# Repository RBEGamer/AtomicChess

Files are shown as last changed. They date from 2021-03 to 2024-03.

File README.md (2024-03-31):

# AtomicChess - The most advanced self playing chess table

prod

## FEATURES

This automated chess table allows the user to play chess using real pieces over the internet with other chess tables or via a web client.
The chess table acts as an opponent and can move the pieces automatically and recognizes the player's moves and sends them to the opponent (chess table or virtual). 

| | Atomic Chess Table |
|:---|---:|
| Recognition figure position | yes, using NFC tags under figures |
| Connectivity | LAN, WLAN |
| Automatic movement of the figures | yes |
| Game Livestream | yes |
| Game history and player scoring | yes |
| Cloud connection (online games) | yes, central gameserver and matchmaking |
| Parking position for eliminated figures | yes |
| Stand-alone functionality | yes, using stockfish-11 (player profile dependent playing strength) | 
| Special features | voice control (Amazon Alexa), DGT3000 chess clock integration, customizable figures |

### OTHER PROJECTS COMPARISON

#### COMMERCIAL PRODUCTS

| | Square Off-Kingdom | Square Off-Grand Kingdom | DGT-Smart Board | DGT Bluetooth Wenge |
|:---|---|:---:|:---:|---:|
| detection figure position | no (manual) | no (manual) | yes | yes |
| Dimensions (LxWxH) | 486mm x 486mm x 75mm | 671mm x 486mm x 75mm | 540mm x 540mm x 20mm | 540mm x 540mm x 20mm |
| Connectivity | Bluetooth | Bluetooth | Serial | Bluetooth |
| automatic movement of the figures | yes | yes | no | no |
| Game Livestream | yes | yes | yes | yes |
| Cloud connection (online games) | yes (App) | yes (App) | yes (PC) | yes (PC + App) | 
| parking position for eliminated characters | no | yes | no | no |
| stand-alone functionality | no (App required) | no (App required) | no (PC) | no (PC) | 
| special features | battery for 30 games | battery for 15 games | - | -  

#### OPENSOURCE PROJECTS
| | Automated Chess Board | Automated Chess Board | DIY Super Smart Chessboard |
|:---|:---:|:---:|---:|
| Figure Position Detection | no (manual) | yes (camera) | no |
| dimensions (LxWxH) | no specification | no specification | 450mm x 300mm x 50mm  |
| connectivity | USB (PC required) | WIFI | |
| automatic movement of the figures | yes | no | | |
| game livestream | no | no | |
| cloud connection (online games) | no | no | yes |
| Parking position for eliminated figures | no | no | no |
| stand-alone functionality | no (PC required) | yes | yes |
| special features | - | voice control | train display (LED matrix)  | |

## Integration of an embedded system into a cloud infrastructure using the example of an autonomous chess table

**NOTE**
This project is my bachelor thesis in computer science. The thesis (german) with details is also available in this repository.

ATC_PROD_TABLE_FINAL_IMG_orig

### Abstract

The goal of the work is to develop an autonomous chess table, which is able to move chess pieces autonomously and to react to user interactions. The core question of the thesis thus relates to the verification of the feasibility including the creation and implementation of an embedded system and a cloud infrastructure. The focus is especially on the programming of the embedded system and the interaction of this with a server accessible from the Internet, which serves as an intermediary between different manholes and other end devices.

First, the approaches existing at the time and their implementation are examined. Here, particular attention was paid to illustrating the limitations of existing systems and comparing them to functions that only apply to this project. From the results, the requirements of the autonomous shaft table are derived, which are to be implemented in this work.

Subsequently, two prototypes were implemented iteratively one after the other, which differ strongly from the mechanical design as well as the electrical one. The developed software, on the other hand, was developed modularly so that it can be used on both prototypes. The different designs are due to the fact that in the first iteration of the autonomous chess table, after an endurance test, numerous potential improvements were identified. This led to a complete redesign in the second iteration and thus an autonomous shaft table was developed, which fulfills all requirements.

Basically, it should be noted that the result of the work is not a finalized product, but a structural prototype. Further tests, such as usage statistics or safety tests, would have to be carried out before the shaft table can be considered a commercial product.

The system and especially the implemented cloud service can be accessed and extended online. Among other things, this allows building your own table using the AtomicChess system, but also integrating other components. Experienced developers can thus expand the game at will or even add to other games. The mechanics and game management designed for the project can accordingly also be used for various other table board games.

### PAPER PDF

`./documentation/atomicchess_thesis.pdf`

### CITE

```tex
@software{Ochsendorf_Marcel_AtomicChessBA_2021,
author = {Ochsendorf, Marcel},
license = {GPL-2.0},
month = {9},
title = {{Integration of an embedded system into a cloud infrastructure using the example of an autonomous chess table}},
url = {https://github.com/RBEGamer/AtomicChess},
version = {1.0.0},
year = {2021}
}
```

## PICTURES


 


## IDEAS

* chess.com & lichess.org integration
* possible target position lights

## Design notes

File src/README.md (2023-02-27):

# SRC

## FOLDER STRUCTURE

* src_atctest => Contains a simple Buildroot Test Package
* src_buildroot => Contains the buildroot source with docker build scripts
* src_ci => Contains the Jenkins server and configuration files
* src_controller => Contains the main chess table controller
* src_marlinfw => Contains the firmware for the used SKR1.3 and SKR1.4 motor controller boards
* src_mechanic => Contains all CAD files for the different hardware revisions
* src_server => Contains the complete game server, player ai server and the CI setup
* src_shared => Contains all used 3rd party libraries and the custom made IPC library (guicommunicator)
* src_thesis => Contains the thesis document and a thesis publishing server
* src_dgt3000chessclockextention  => Contains the DGT 3000 Chess-Clock extention software for the DGT PI
* src_userboardcontroller  => Contains the atmega328p nfc reader to serial bridge software used for prod 1,2 models

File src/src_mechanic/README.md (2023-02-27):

# SRC_MECHANIC

This folder contains all mechanical drawings (CAD, SVG, STL files). During development three hardware revisions were developed.

## USED TOOLS

* FDM 3D Printer (Ender 3 Pro, Ender 2)
* Soldering Iron (Weller PU81)
* Hex Keys / Allen Wrenchs
* Hotglue Gun

* [OPTIONAL] SLA 3D Printer (Elegoo Mars 2 Pro) for custom Chess Figures 
* [OPTIONAL] Crosscut Saw (Bosch GCM8) for Item cutting
* [OPTIONAL] Lasercutter (K40E) for acryl chess board markings

## HARDWARE REVISIONS

* `HARDWARE_PROD_V2` => Contains the final version with CoreXY configuration. For this a control board (SKR) with Marlin needed. Firmware in `src_marlinfw`. 

* `HARDWARE DEV` => Contains the IKEA Lack Table version of the chess table using self developed hardware and pcbs and a two coil system.

## NOTES

The software `atc_controller` and `atc_qtui` is compatible with all versions of the hardware.
The only difference is the configuration file `atccontrollerconfig.ini` which need modification to the new board size and controller type (SPI or Marlin).
If not configuration file is present the table automaticly generates a default one for the selected version.

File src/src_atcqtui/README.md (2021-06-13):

# AtomicChessOS

# BRANCH - QTUI

This folder contains the QT5 User Interface which is running on the RaspberryPi Display.

## REQUIREMENTS
For this chapter the following requirements must be met:

* Crossplattform toolchain and target images is build. The `/buildroot/output/host` folder is accessable on the development system.
* Embedded device is flashed with the image and reachable over SSH.
* `Qt Creator >= 4.10` and `Qt Design Studio` is installed on the development system (`>= Ubuntu 16.04`).

## TASK OF THE UI

The main purpose of the ui is the management of a gameand should not stand in 
* simple editable
* provide simple menu structure with max two menu layers
* player browser
* start game /stop game

### MENUS

## Qt

### WHY Qt

### QML

#### QML COMPONENTS

Every element begins with the type name of the qml component `Text {`, in this case its a label component.
The following block can contain at least a `id` attribute, but can have many more attributes.
The most common attributes are the  position on the screen `x`, `y` and a size `width`, `height`.
These attributes are automaticly added, if an element is created with the visual editor in `Qt Creator` or `Qt Design Studio`.

In case of the label, some additional attributes are nedded.
The `text` attribute, sets the visibal text of the label and the font size can be changed with the `font.pixelSize` attributes.

```qml
Text {                                          //QML TYPE, Text means label                                          
            id: hb_label                        //ID OF THE ELEMENT
            objectName: "hb_label"              //NAME TO ACCESS THE LABELS ATTRIBUTES IN C++ BACKEND
            x: 318                              //POSITION IN SCREEN COORDIANTES
            y: 18                   
            width: 164                          //SIZE
            height: 34
            text: qsTr("MAIN MENU")             //VISIBLE TEXT
            visible: true                       // HIDE| SHOW ELEMENT
            font.pixelSize: 30                  //FONTSIZE OF THE TEXT
        }
```

The next element which is heavily used in the UI for the project, is a simple button.
In addition to the already shown attributes, a new section called `Connections` was added to the element.
Most of the qml types can emit events, if a state of the element changes.
For example, the button can emit the `onClick` event, if the user clicked on the button.
A eventlistener can be registered in a `Connections {` block.
This block needs a `target` attribute, which value is the `id` of the element, the events should be processed.

The eventlistener itself is a function, which has the name of the event `onClick`.
The systax is JavaScript based and a small subset of the JavaScript language in functions is supported.

```js
onClick: {
            var arr = ["My", "Label"] //JS ARRAY
            hb_label.text = arr[0] + arr[1] //ACCESSING ATTRIBUTE OF AN OTHER QML ELEMENT
            console.log("CLICKED!") //JS EXPRESSION
        }
```
A complete QML Javascript refrence guide can be found on the Qt 5 Site.
[QML_JS_REFERENCE](https://doc.qt.io/qt-5/qtqml-javascript-expressions.html)

The goal of our button example is if the user clicked on the button, the label with id `hb_label` should be displayed.
Also a function from an other QML Componente should be called, in this example the `main_menu` component is our C++ backend.

```qml
Button {
            id: hb_button
            x: 731
            y: 4
            width: 61
            height: 61
            text: qsTr("BUTTON NAME")
            //REGISTER EVENT HANDLERS
            Connections {
                target: hb_settings_button      //FOR WHICH ELEMENT ID IS THE CONNECTION             
                function onClicked(_mouse){     //EVENT HANDLER FOR THE CLICK EVENT
                    hb_label.visible = true     //MODIFY OTHER QML ELEMENTS
                    main_menu.lb_settings_btn() //CALL A C++ BACKEND FUNCTION (main_menu is the QML instance of the C++ backend)
                }
            }
        }
```

### MOCKUP

For the first mockups, the tool `Balsamique Mockup 3` was used to create a wireframe model of the menus.
Though the requirement that the userinterface should be simple to create and operate, only simple GUI element was used (like buttons, labels, icons).
So the userinterface can be adapted in every other UI framework too.
It also habe to be simple to use for the user and every menu should only present the most important elements.

The UI conzept offers the users to do the following things:

* Start a random game
* Start a game with selected user
* Overview of game progress and state
* Abort game
 
After deciding which elements are necessary to map this functionality, a simple mockup of the user interface was created.

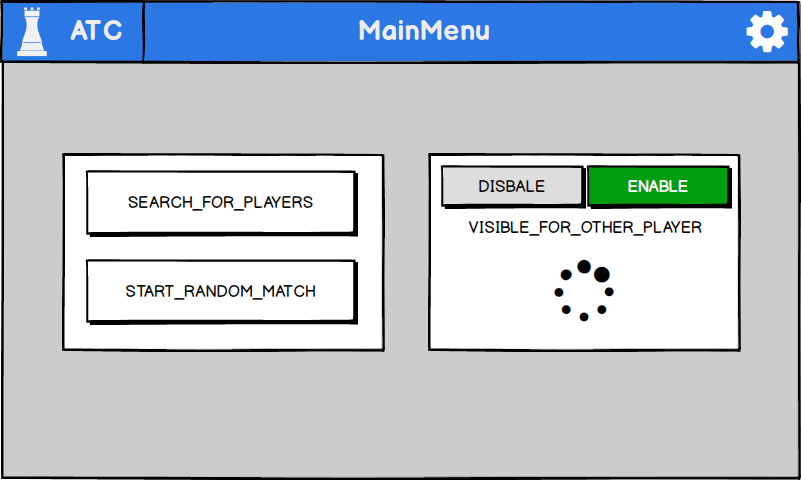
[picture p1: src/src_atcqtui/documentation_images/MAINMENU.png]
MOCKUP_MAIN_MENU


For example, this is the mockup of the MainMenu. It allowes the player, to start a random game, get the players list and a spinning indicator was used to show the state of the game search funktion.

The gearbox icon, redirects the user to the settings menu. This menu offers basic options to interact with the table.
In a normal usage situation this settings menu is not important, but it is mostly used for maintenance.
The settings menu is accessable in every other menu and the back button, redirects the user back to the last menu showed before opening the settings menu.

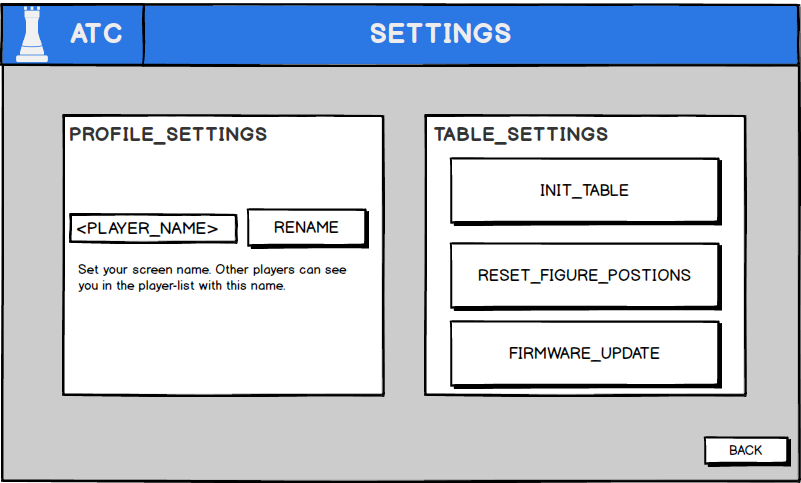
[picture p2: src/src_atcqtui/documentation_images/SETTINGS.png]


A general information menu was added, which shows the table software version, its hardware id (used for communcation with the cloud backend).
For debug reasons the last internal errormessage can be shown here.

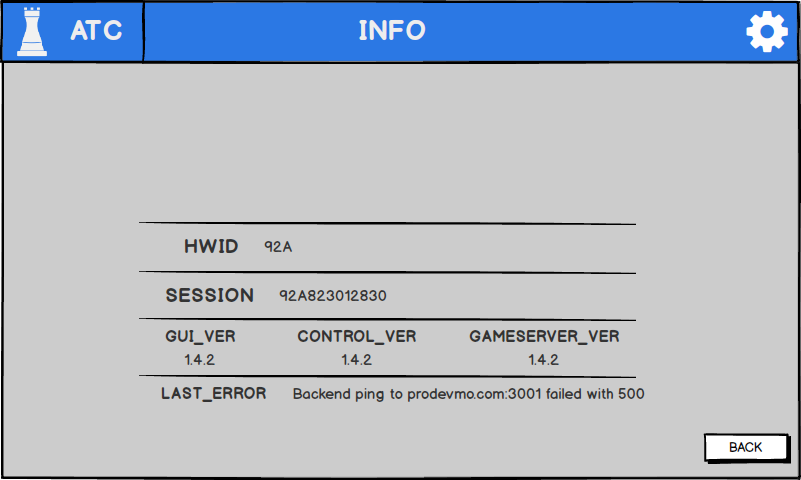
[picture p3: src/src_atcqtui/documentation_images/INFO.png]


This are only three example menus created for the user interface.
After creating the mockups, `Qt Design Studio` was used to convert the Mockup into an `QML` represenation

### Qt Design Studio

`Qt` offers several different tool to create a user interface. In this case the `Qt Design Studio`, was used in the first step of implementing the UI form the mockup. It has some advantages over the `Qt Creator`, reagarding the design workflow. It is for example possible to direclty import Adobe Photoshop files, this feature was used for the creation of the icons used in the interface. No manually export of the icon from Adobe Photoshop and reimporting into Qt was needed.
It supports live preview of the design as an running application, no compilation needed for reviewing the UI.

The software uses a simple drag&drop system for elements, like buttons, labels and self designed components. The element can be placed on a empty screen to build the ui from the ground up. It provides integration for the `QtQuickControl II` component presets, which includes some more advance ui element like the animated spinner or progress bars.

While building the UI in the software, the equivalent QML code is generated which corresponds in an `.qml` file.
The QML file can now be loaded into a `Qt Quick - Application` project inside of the `Qt Creator` software. 

## Qt Creator

* works without QtCreator but offers features espacially for editing C++ and QML files together
### PROJECT SETUP
* simply clicking ok; but choose qmake
* generate main.cpp with qml loading code ; and a basic qml file 
### TOOLCHAIN SETUP
* path setup
### DEVICE SETUP
* add device with ip address

## QML `objectName` ATTRIBUTE
It is also possible to edit the QML code and add new QML components inside of `Qt Creator`, which offers a QML visual editor.
Here all object which are designed to be changed with C++ code, become a unique name. This happens inside of the QML code with the `objectName` attribute.

For example the content of the version label on the info menu should be changeable, so its gets a unique name with 
```qml
Text {
            id: is_hwid_label
            objectName: "is_hwid_label"
            x: 358
            y: 54
            color: "#ffffff"
            text: qsTr("HWID")
            font.pixelSize: 30
        }
```

With the `objectName` attribute set, it is possible modify other attributes inside of the element.
In the following C++ function is taken from the `menumanager.cpp` which is the C++ backend class between the QML and the `InterProcessCommunication`.
The funktion changes the visible attribute of an element, which is searched with the `objectName` attribute.

```c++
//menumanager.cpp
void MenuManager::set_visible_element(QString _name, bool _state){
    QObject* obj = this->parent()->findChild<QObject*>(_name);
    if(obj){
        obj->setProperty("visible",_state);
    }else{
        qInfo()<< "cant get element" << _name;
    }
}
```
## QML C++ BACKEND

As mentioned above, the UI is controlled by a C++ backend, it connects the QML UI with the `InterProcessCommunication` class.
This backend can be used as a normal QML Component, but allowes all C++ feature can be used to control the UI.
The backend is a normal C++ Class, but it have to inherited from `QObject`.

```c++
//menumanager.h
#include <QObject>
class MenuManager: public QObject
{
```

After creating the class files `menumanager.h` and `menumanager.cpp`, the last step is to register the new created class as a usable QML component.
This happend in the `main.cpp` file directly after bevore loading the QML file with the `qmlRegisterType` function call.

```c++
//menumanager.h
#include "menumanager.h"
int main(int argc, char *argv[])
{
            QGuiApplication app(argc, argv);
            QWindow window;
            window.setBaseSize(QSize(800,480));
            ...
            ...
            
            //REGISTER THE TYPE MenuManager WITH THE NAME MenuManager AND VERSION 1.0 AS QML TYPE WITH NAME MenuManager           
            qmlRegisterType<MenuManager>("MenuManager",1,0,"MenuManager");
            
            //LOAD QML FILE AND DISPLAY IT
            QQuickView view;
            view.engine()->addImportPath("qrc:/qml/imports");
            view.setSource(QUrl("qrc:/qml/WINDOW.qml"));
            ...
            ...
```

The last step required is to use the new created QML type in the QML file `WINDOW.qml` of the UI.

```qml
//qml/WINDOW.qml
Rectangle {
    id: window
    objectName: "window"
    width: 800
    height: 480

    //CREATE AN ELEMENT OF QML TYPE MenuManager    
    MenuManager{
        id:main_menu
    }
```
Now every function inside of the UI can call functions in the C++ backend by using the ID `main_menu.<FUNCTION>()`.

### ACCESS MODIFIERS TO WORK WITH THE UI
In the headerfile `menumanager.h` function can be declared with the access modifiers, for example`public` or `private`.
In the Qt C++ there are other modifiers avariable, espacially for connecting with QML.

The mainly used modifier for this project is the `public slots` modifiert. Each function declared in this section can be called from the QML side.

```c++
//menumanager.h
class MenuManager: public QObject
{
public slots:
            void trigger_login_event_button(); //call if login button is pressed
```

For example the obve delcared function `trigger_login_event_button` should be called with a button in the QML UI is pressed by the user.

```qml
qml/WINDOW.qml
Button {
            id: hb_button
            ... //OTHER ATTRIBUTES
            //REGISTER EVENT HANDLERS
            Connections {
                target: hb_settings_button      //FOR WHICH ELEMENT ID IS THE CONNECTION             
                function onClicked(_mouse){     //EVENT HANDLER FOR THE CLICK EVENT
                    
                    main_menu.trigger_login_event_button() //CALL A C++ BACKEND FUNCTION (main_menu is the QML instance of the C++ backend)
                    
                }
            }
        }
```
[SIGNALS_SLOTS_QT](https://doc.qt.io/qt-5/signalsandslots.html)

### GET EVENTS FROM QML COMPONENTS | REACT TO BUTTONS
With the `public slots` modifiers above, its is now possible to react to event from components.
For example if the user presses the login button.
In the `mainmenu` class, for each action is a function declared, mostly for buttons an their `onClick` event.

```c++
//menumanager.h
class MenuManager: public QObject
{
...
...

public slots:
// ----- HEADLINE BAR ---- //
    void lb_settings_btn();         //ONCLICK EVENT FOR SETTINGS ICON
    void lb_info_btn();             //ONCLICK EVENT FOR INFO ICON                     
    // ----- LOGIN/START ----//
    void ls_login_btn();            //ONCLICK EVENT FOR START BUTTON                       
    ...
```

Every functions triggers a event, which are send to the rest of the system by using the `Inter Process Communication` class.

```c++
//menumanager.cpp
void MenuManager::ls_login_btn(){
    qInfo() <<"ls_login_btn"; //DEBUG MESSAGE
    
    //CREATE EVENT WITH ACTION TYPE (GUI_ELEMENT::BEGIN_BTN) AND THE TYPE OF EVENT (GUI_VALUE_TYPE::CLICKED)
    guiconnection.createEvent(guicommunicator::GUI_ELEMENT::BEGIN_BTN, guicommunicator::GUI_VALUE_TYPE::CLICKED);
}
```

### MODIFY QML COMPONENTS | SWITCHING BETWEEN MENUS

Now its possible to react to user events, but the other direction, to send events to the gui is needed.
To display the current gamestate or switching between menus.

The `visible` attributes of an element, defines if the element is visible on the ui or not.
In the case of the UI for this project. Each menu is placed inside of an container.
If the user open a specific menu, all other menus will be hidden by setting the `visible` attribute to `false`, ecept of the target menu.

For this purpose each menu container has its own `objectName` attribute.

* `mm_container`, is the main menu container
* `ss_container`, is the settings menu container
* `ls_container`, is the start screen container

To finally switch the a menu the function `switch_menu(QString _container_name)` can be used, for simple menu switching.
It poulates a variable called `last_menu_opened`, this stores the menu name the user comes from and makes its possible to switch back to the previous menu.
This functionally comes handy, for the settings menu, which can be opened from every other menu and by closing the settings menu the user redirect back to the previous menu.

```c++
switch_menu("ls_container"); //SHOW LOGIN MENU
switch_menu("ss_container"); //SHOW SETTINGS MENU
switch_menu(last_menu_opened); //SWITCH BACK TO LOGIN MENU (= PREVIOUS MENU)
```

For this menu structure it is sufficient to store only the previous menu.
A queue is used to enable navigations with deeper menu structures.

```c++
//menumanager.h
QStack<QString> menu_visist_history;
QMap<QString, int> menu_levels;
QString current_menu = "";

//menumanager.cpp
//ENTER MENU
void enter_menu(QString _name){
            previous_menus.push(current_menu)
            current_menu = _name;
            switch_menu(current_menu);
}

void leave_menu_to_previous(e){
    qInfo() << "go_menu_back";
    if(menu_visist_history.isEmpty()){ //CHECK IF PREV MENU EXISTS
        return;
    }
    QString tmp = menu_visist_history.pop(); //LOAD PREV MENU
    switch_menu(tmp); //SWITCH TO PREV MENU
}

void MenuManager::switch_menu(QString _screen){
    //SAVE ONLY THE CURRENT SCREEN TO THE QUEUE IF WE MOVE A LEVEL UP IN SCREEN TREE
    if(menu_levels.contains(_screen) && menu_levels.contains(current_menu_opened) && menu_levels[_screen] > menu_levels[current_menu_opened]){
    menu_visist_history.push(current_menu_opened);
    qInfo()<< "added to history " << current_menu_opened;
    }
    current_menu_opened = _screen;
    //...
    //...
}
```

### INTER PROCESS COMMUNICATION

The whole `Inter Process Communication` acronym `IPC` functionallity was implemented in `guicommunicator` class, which is located in the `SHARED` folder.

The `guicommunicator` offers a bidirectional communication between processes, which is needed for communcation between the UI and the controller software.
There a already implementations for such a behavior like `gRPC`, `librpc` or message queues like `ZeroMQ`.

??
TYPES
??

For this project a own implementation for the `IPC` concept was created. One reason for that was the integration into the buildroot system.
`gRPC` has a bug in the package compilation with buildroot.
A issue on the `libabseil-cpp` library GitHubPage, was opended.

ISSUE

An alternative to `gRPC` is the `ZeroMQ` library, which offers a lightweight message queue concept.
Buildroot offers libraries for building the `ZeroMQ` message broker and different client libraries `libzqm`.
Both packages are build into the toolchain.

`ZeroMQ` is designed for performance message transportation (10.000 message in 15ms) ,which is not needed for this project.

[ZeroMQ_PERFORMANCE](http://wiki.zeromq.org/area:results)

The `guicommunicator` class offers two methods for the message transport:

* `ZeroMQ`, by using the define `USE_ZMQ_AS_IPC`
* `Webserver`, by using the define `USE_WEBSERVER_AS_IPC`

The webserver method is implemented by using a http client and webserver instance for each direction.
This method was used, because the UI was designed before the other software parts.
So as other 'process' a simple http client can be used.

The codebase is for the UI and the Control apllication is the same.
There are some differences, Qt uses its own string type `QString` and uses other debug features `QDebug()`.
For this cases defines are used to implement the same function for both the Qt version and non Qt version.
The deine `USE_QT` is set in the project settings of the Qt project.

```c++
//SHARED/guicommunicator.h
#ifdef USES_QT
            #include <QString>
            #include<QDebug>
            #include <QThread>
            #include <QMutex>
#else
            #include <string>
            #include <mutex>
            #include <iostream>
            #include <thread>
#endif
```

In the implementation of the functions, the define was used.

```c++
//SHARED/guicommunicator.cpp
	void guicommunicator::createEvent(GUI_ELEMENT _event, GUI_VALUE_TYPE _type) {
		guicommunicator::createEvent(_event, _type, (std::string)"");
	}
#ifdef USES_QT 
	void guicommunicator::createEvent(GUI_ELEMENT _event, GUI_VALUE_TYPE _type, QString _value) {
		guicommunicator::createEvent(_event, _type, _value.toStdString());
	}
#endif
```

The `guicommunicator` class offers two main methods:

* `createEvent(_event, _type, _value)`, to send a event to the other process.
* `GUI_EVENT get_gui_update_event()`, which returns the received events

The library uses a thread for sending and received message packets, so start and stop methods are implemented.
The calling of this methods are only necessary if the instance of class want to receive messages.

* `start_receive_thread`, start receive thread.
* `stop_receive_thread`, stop receive thread.

After receiving a message (from webserver or `ZeroMQ`), the message will be checked and converted into the `GUI_EVENT` struct.
Allo received messaged will. be queued up into an queue datastructure and can pulled of the queue by using the `get_gui_update_event` method.
The insertion and reading of the queue, is secured with an binary semaphor to avoid a condition race in the critical section.
The critical section is in this case, the read/write access to the queue.

* TYPES OF EVENTS

* PACKING OF THE MESSAGES -> protobuf

##### Protobuf
* message types
* needed information
* generation of the .proto file to cpp code
* location of the files in shared folder

##### Webserver
* advantage for debugging
* zeromq not wokring

### DEPLOYMENT

* using buildroot pacakge
* simply use qmake to gerneate makefile
* and run makefile in buildroot
 
## CONCLUSION

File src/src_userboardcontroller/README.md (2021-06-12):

# SRC_USERBOARDCONTROLLER

Contains the Arduino-Sektch for the PN532 to Seriell converter, to connect the nfc reader to the controller via usb

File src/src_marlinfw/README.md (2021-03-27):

# SRC_MARLINFW

This directory contains the used Marlin-Firmware for the SKR1.3 (HWREV_PROD1) and SKR1.4_TURBO (HWREV_PROD2).

The simplest way to compile and flash the narlin firmware is with Visual Code and the following installed Plugins:

* PlatformIO
* Auto Marlin

## PRECOMPILED MARLIN FIRMWARE

Simply copy the .bin file to the SD Card of the board, or via the USB mount.

* SKR1.3 => ./SKR_V1.3_BOARD_FIRMWARE/ATC_HWREV_PROD1_MODIFIED_FIRMWARE/
* SKR1.4_TURBO => ./SKR_V1.4_BOARD_FIRMWARE/ATC_HWREV_PROD1_MODIFIED_FIRMWARE/

## MARLIN SOURCE PROJECTS

* SKR1.3 => ./SKR_V1.3_BOARD_FIRMWARE/BTT SKR V1.3/firmware/Marlin-bugfix-2.0.x
* SKR1.4_TURBO=> ./SKR_V1.4_BOARD_FIRMWARE/BTT SKR V1.4/firmware/Marlin-2.0.x-SKR-V1.4-Turbo/

## USED GCODE COMMAND

The controller software uses the following GCode commands. Some are optional for example the M150 command that setup the RGB Strip.

### REQUIRED COMMANDS
* `G21` - set units to mm
* `G90` - absolute positioning
* `G28` - home axis
* `M280` - set servo
* `G0` - move linear
* `M400` - wait for action finished

* `M260 M261` - i2c read write (for nfc read)

### OPTIONAL COMMANDS

* `M84` - disable steppers
* `M502` - reset eeprom
* `M500` - write config to eeprom
* `M92` - set steps/mm
* `M150` - set rgb led strip color

## IMPORTANT CONFIGRATION SETTINGS IN MARLIN-FW

The main marlin configuration files are the `Configuration.h` and `Configuration_adv.h` located in the the Marlin folder.

For the ATC Project the following settings are changed in comparision with the default config.

### Configuration.h

* `0615 | #define COREYZ //ON HWREV_PROD2`  
* `0664 | #define X_MIN_ENDSTOP_INVERTING true // Set to true to invert the logic of the endstop.`
* `0665 | #define Y_MIN_ENDSTOP_INVERTING true // Set to true to invert the logic of the endstop.`
* `0750 | #define DEFAULT_AXIS_STEPS_PER_UNIT   { 80, 80, 400, 93 } // FOR HWREV_PROD2 USE { 100, 100, 400, 93 }`
* `1096 | #define INVERT_X_DIR false //INVERT ENDSTOP SIGNAL`
* `1097 | #define INVERT_Y_DIR false` 
* `1132 | #define X_BED_SIZE 700`
* `1133 | #define Y_BED_SIZE 700`
* `1404 | #define HOMING_FEEDRATE_XY 600 //LIMIT THE HOMING FEEDRATE`
* `2359 | #define NEOPIXEL_LED //ENABLE NEXOPIXEL LED SUPPORT`
* `2365 | #define NEOPIXEL_PIXELS 60       // Number of LEDs in the strip.`
* `2412 | #define NUM_SERVOS 1 // Servo index starts with 0 for M280 command ON SKR BOARD THE SERVO PIN IS P2_00`
* `2417 | #define SERVO_DELAY { 500 } //(ms) Delay  before the next move will start`

### Configuration_adv.h

`2797 | #define EXPERIMENTAL_I2CBUS //ENABLE I2C Master`

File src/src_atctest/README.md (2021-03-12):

# ATC_TESTPACKAGE

This program is a compile and install test for the modified buildbrocess of the buildroot framework.
This folder will be fetched from the buildroot atc_testpackage package configured in buildroot.

Please see the `./src/src_buildroot/packages/atctp` directory for the actual build configuration.

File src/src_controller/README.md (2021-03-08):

# AtomicChessOS

# ATC CONTROLLER

The controller is the main system on the embedded device that controls the hardware of a ATC Table

* Motor Control
* Communcication with the Server
* Communication with the UI running on the device
* Chess Figure Movement Algorithm

For this software component, we are using a Windows and Visual Studi environment for developing the software.
Our embedded system is a linux device, so we have to build the application for the linux environment running on the emmbedded device.
For this task, the prevously build buildroot toolchain is used.
A software plugin called VisualGDB for Visual Studio, enable Visual Studio to use the linux toolchain over a remote linux system, in order to build and deploy the application.

## REQUIREMENTS

* windows pc for development
* linux pc with buildroot toolchain
* embedded system for deployment

## SETUP A PROJECT USING VISUAL STUDIO AND VisualGDB

### REQUIREMENTS

On the development windows pc is the following software installed:
* Windows 10 Pro x64
* Visual Studio 2019 (Community or Enterprise)
* VisualGDB Plugin (Version 5.5, Linux Edition)
* A SSH Client (MobaXterm Personal Edition)
* git (Gitkraken)

### LINUX BUILD SYSTEM

On the linux build system, the VisualGSB plugin builds the project.
The system is a `Intel Nuc 10`, mini pc, with a stock `Ubuntu 20.04` installed.
One the machine are all package requirements for building the buildroot toolchain installed (see buildroot chapter).

After cloning the repository `$ git clone -b buildroot git@github.com:RBEGamer/AtomicChessOS.git ./atc_buildroot` and switched to the `buildroot` branch, the build process of the toolchain was invoked using the build script `$ ./atc_buildroot/src/src_buildroot/buildroot/build.sh`.

After building the  toolchain is completed, the further configuration work can be done on the windows development pc.
Its nessessary for the linux build system to allow SSH connections.
Its may required to install the OpenSSHServer uisng `$ sudo apt install openssh-server`.

The VisualGDB plugin requires some extra packages on the build pc:

* `$ sudo apt-get install socat`

Now the configuration of the linux build pc for the VisualGDB plugin is complete.
The next step, is the setup of the embedded system for deployment.

### EMBEDDED SYSTEM DEPLOYMENT

Afer building the sources into an executable, the final binaries will be copied to the embedded system.
The embedded system is flashed with tha latest image build by buildroot.

In order to setup the VisualGDB Project, its nessessary that the embedded device can be accessed over SSH.

#### MAKEFILE MODIFICATIONS
* buildroot build oveerrides TARGETNAME AND CONFIG to load a different makefile config in order to use the toolchain generated by buildroot
The different configurationa are stored in different .mk files that will be includes by the Makefile.
THe `debug.mk` configuration contains theVisualGDB Configuration that allows the Visual Studio Plugin to use the remote toolchain on the linux server and can only build by over the visual gdb plugin.
The `release.mk` configuration is used to build the controller apllication with the buildroot framework. It used the compiler executable paths defines by $CC. $LD enviroment variables and build the program with release flags and without any debug symbols. All used libraries are linked staticly.

## THIRD PARTY LIBRARIES

The ATC_Controller software uses serveral different third party libraries, escacially for http requests and json parsing.
* `https://github.com/nlohmann/json#serialization--deserialization`, json parsing.
* `https://github.com/yhirose/cpp-httplib`, http/https requests.
* `https://github.com/Neargye/magic_enum`, enum handling.
* `https://github.com/emilk/loguru`
A copy of the used versions, are located in the controller software directory.

# CONTROLLER OVERVIEW

## MOTOR DRIVER
## BOARD CLASS

## CHESS PIECE
### NFC TAG CONTENT GENERATOR
Each figures NFC tag is ued to identify the figure. For easy usage of the NFC tag, it is formatted into the NDEF format, so its simply possible to program the NFC tags with an mobile phone. The tag contains a ndef `text record` with a string to identifiy the type of figure (three bits), color (one bit) and a counting number (four bits). A combination of all three attributes make the figures id unique to the system. For the automatic unique ID generation, a html page `ChessFigureIDGenerator.html` was created to automaticliy generate all ID for a complete chess board.
Only one byte is stored in the record of the text record and so only 10bytes are used on the NFC tag.

* MSB [7,6,5,4,3,2,1,0] LSB 
* MSB [TYPE,TYPE,TYPE,COLOR,ID,ID,ID,ID] LSB 

For reading the NFC tag with the PN532, the program only reads the first NDEF record and parses the text record data to get the figure type. With this system it is possible to expand the system further and store more data on the NFC tag, by adding more NDEF records.

On the controller side two functions were created to generate the unique ids and read them back.

```c++
  ChessPiece::FIGURE fig;
	fig.figure_number = 1;
	fig.color = ChessPiece::COLOR_BLACK;
	fig.type = ChessPiece::TYPE_KNIGHT;
  
  //GENERATE ID FROM STRUCT
  uint8_t UNIQUE_ID = ChessPiece::figure2NDEF(fig);
  
  //PARSE UNIQUE_ID BACK TO A STRUCT
  ChessPiece::FIGURE back = ChessPiece::NDEF2Figure(UNIQUE_ID);
  
````
* IMAGE

## CONFIG AND CALIBRATION

The system uses a config file located in the filesystem `/usr/ATC/atccontroller.ini`.

### CALIBRATION

In order to calibrate the mechanic, several entries in the config file has to be changed.

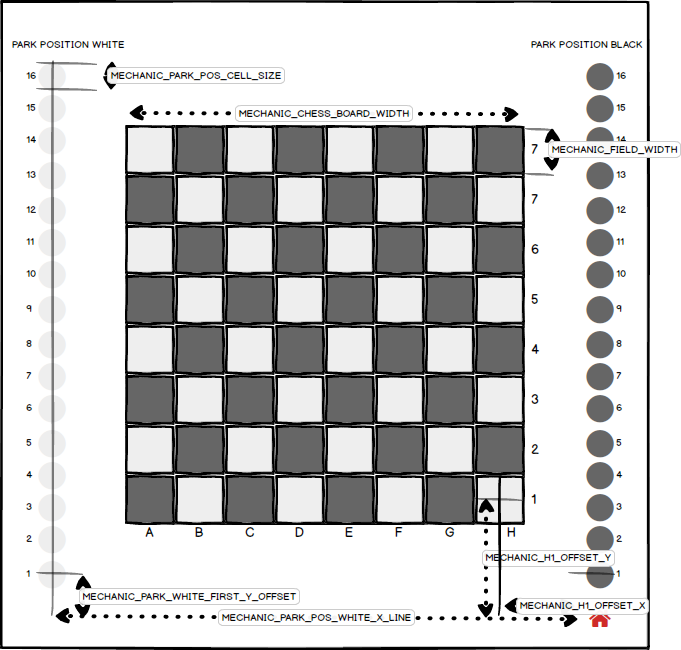
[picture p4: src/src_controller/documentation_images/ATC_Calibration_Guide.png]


### Chess Piece Movement Algorithm

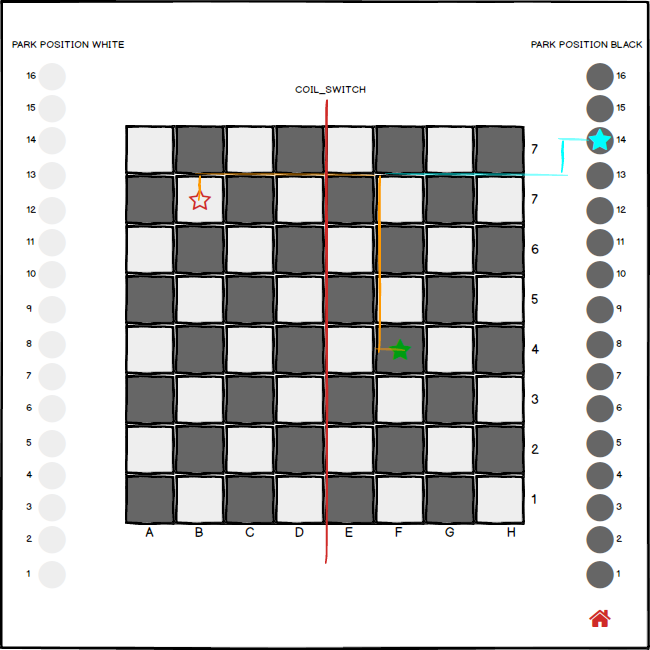
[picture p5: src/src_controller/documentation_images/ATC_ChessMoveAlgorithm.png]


#### BASIC MOVEMENT PROCEDURE

*move 
##### BOARD <-> BOARD

##### PARK_POSITION <-> BOARD || BOARD <-> PARK_POSITON

##### ALGORITHM IMPROVEMENTS

* queue movement all movementinstructions needed for a move, send them combinded to the motor driver
* send coil change event only if changed, SPI Implementation needs time (about 0.5 Secs with the wait ACK)
*

#### PIECE MOVE TIME

| ALGORITHM_V1_TRAVEL_TIME [s] 	| ALGORITHM_V2_TRAVEL_TIME [s] 	| TRAVEL_DISTANCE [FIELDS_DIAGONAL] 	|
|---	|---	|---	|
| 7.20 	| 2.56 	| 1 	|
| 11.56 	| 6,20 	| 3 	|
| 12,27 	| 7,06 	| 5 	|
| 14,39 	| 6,56 	| 8 	|

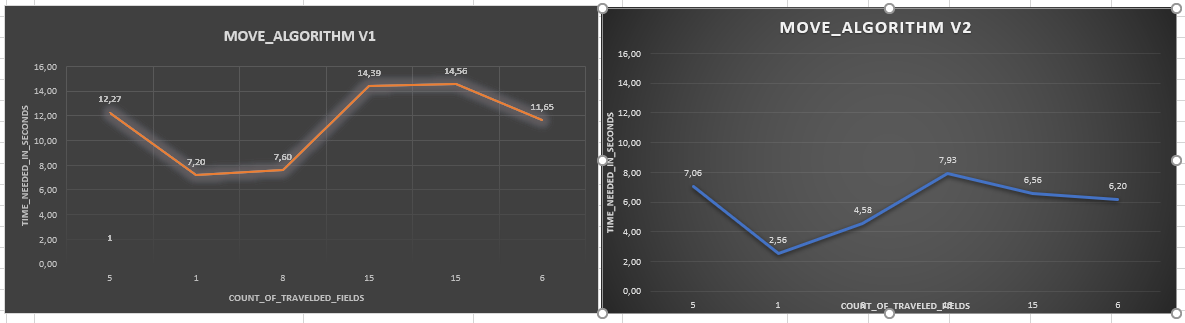
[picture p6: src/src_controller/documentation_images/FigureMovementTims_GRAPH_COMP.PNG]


### MOVEMENT SPEED COMARPISION HARDWARE V1 / V2
* gocde slower nicht

#### [LINUX] HANDLING DIFFERENT 
The simplified hardware design of the projects uses two USB2Serial adapters to connect the SKR1.3 Stepper Driver Board and the User-Move Dector with the Embedded System. All serial deives will be mount under the `/dev/ttyXXX` path and the the squence can be differ after each reboot. In order to prevent this, it is possible to mount a usb device with a Vendor and Product-ID to a specified path using a custom udev roule.
For each rule, the Vendor and Product-ID is needed, for this commands like `lsub` or `usb-devices` and output the relevant information for each usb device attached.
```
$ usb-devices

T:  Bus=03 Lev=02 Prnt=02 Port=02 Cnt=03 Dev#= 11 Spd=12  MxCh= 0
D:  Ver= 2.00 Cls=ef(misc ) Sub=02 Prot=01 MxPS=64 #Cfgs=  1
P:  Vendor=1d50 ProdID=6029 Rev=01.00
S:  Manufacturer=marlinfw.org 
S:  Product=Marlin USB Device
S:  SerialNumber=06FF800AAF3D08075C664F58F50020C3
C:  #Ifs= 3 Cfg#= 1 Atr=80 MxPwr=500mA
I:  If#=0x0 Alt= 0 #EPs= 1 Cls=02(commc) Sub=02 Prot=00 Driver=cdc_acm
I:  If#=0x1 Alt= 0 #EPs= 2 Cls=0a(data ) Sub=00 Prot=00 Driver=cdc_acm
I:  If#=0x2 Alt= 0 #EPs= 2 Cls=08(stor.) Sub=06 Prot=50 Driver=usb-storage
```
During development, several different board are used to control the different hardware sections.
These can be divided into two main groups :

* `Stepper-Controller` - For controlling the Stpper-Drivers, Endstop, Coils/Servo
* `User-Move-Detector` - To interface the hall-sensor array, to detect a manual move of the figures.

In the following table, the Vendor/Product-IDs from some tested boards are listed below:

| Product | SUBSYSTEM | Vendor-ID | Product-ID | SYMLINK | Board-Type |
|---|---|---|---|---|---|
| Bigtreetech SKR 1.4 Turbo | tty | 1d50 | 6029 | ttySKR | Stepper-Controller |
| Bigtreetech SKR 1.3 | tty | 1d50 | 6029 | ttySKR | Stepper-Controller |
| Arduino Due [Programming Port]  | tty | 2341 | 003d | ttyUBC | User-Move-Detector |
| Arduino Due [Native SAMX3 Port] | tty | 2341 | 003e | ttyUBC | User-Move-Detector |
| CH340 | tty | 1a86 | 7523 | ttyUBC | User-Move-Detector |
| HL-340 | tty | 1a86 | 7523 | ttyUBC | User-Move-Detector |
| STM32F411 | tty | 0483 | 5740 | ttyUBC | User-Move-Detector |

With these information, is is possible to generate the needed udev rules.
```
$ cat /etc/udev/rules.d/50-usb.rules

...
SUBSYSTEM=="tty", ATTRS{idVendor}=="1d50", ATTRS{idProduct}=="6029", SYMLINK+="ttySKR"
...
SUBSYSTEM=="tty", ATTRS{idVendor}=="0483", ATTRS{idProduct}=="5740", SYMLINK+="ttyUBC"
...
```
This configuration archieves, that any type (of supported) Stepper-Controller-Boards are accessable over the `/dev/ttySKR` symblink.

After the installation of the rules and connection of a SKR1.3 and a STM32F411 (known as STM32-BlackPill), the device directory contains the following entires:

```
ls /dev/tty*

/dev/ttyS27  /dev/ttyS6
/dev/ttyUSB0  /dev/ttyACMA0  /dev/tty25  /dev/tty32  /dev/tty4  /dev/ttyprintk  /dev/ttySKR  /dev/ttyUBC
```
The in the configutation file of the controller file, these tty paths are set and no reconfiguration for different hardware configuration is needed.

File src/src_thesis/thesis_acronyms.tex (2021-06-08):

\makeglossaries
\newacronym{ic}{IC}{Integrated Circuit}
\newacronym{html}{HTML}{Hypertext Markup Language}
\newacronym{js}{JS}{JavaScript}
\newacronym{css}{CSS}{Cascading Style Sheets}
\newacronym{ndefrtd}{NDEF-RTD}{NDEF Record Type Defintion}
\newacronym{http}{HTTP}{Hypertext Transfer Protocol}
\newacronym{https}{HTTPS}{Hypertext Transfer Protocol Secure}
\newacronym{ftp}{FTP}{File Transfer Protocol}
\newacronym{dns}{DNS}{Domain Name System}
\newacronym{aws}{AWS}{Amazon Web Services}
\newacronym{nfc}{NFC}{Near Field Communication}
\newacronym{rfid}{RFID}{Radio-Frequency Identification}
\newacronym{ci}{CI}{Continuous Integration}
\newacronym{cd}{CD}{Continuous Deployment}
\newacronym{iot}{iot}{Internet of Things}
\newacronym{mqtt}{mqtt}{Message Queuing Telemetry Transport}
\newacronym{rest}{REST}{Representational State Transfer}
\newacronym{api}{API}{Application Programming Interface}
\newacronym{cad}{CAD}{Computer-Aided Design}
\newacronym{rpi}{RPI}{Raspberry-Pi}
\newacronym{os}{OS}{Operating System}
\newacronym{vcs}{VCS}{Version Control System}
\newacronym{atc}{ATC}{Atomic Chess Table}
\newacronym{ui}{UI}{User Interface}
\newacronym{gui}{GUI}{Graphical User Interface}
\newacronym{ssh}{SSH}{Secure Shell}
\newacronym{ntp}{NTP}{Network Time Protocol}
\newacronym{sftp}{SFTP}{Secure File Transfer Protocol}
\newacronym{ide}{IDE}{Integrated Development Environment}
\newacronym{ipc}{IPC}{Interprocess Communication}
\newacronym{qml}{QML}{Qt Modeling Language}
\newacronym{dtb}{DTB}{Device Tree Binary}
\newacronym{dtc}{DTC}{Device Tree Compiler}
\newacronym{dtd}{DTD}{Device Tree Document}
\newacronym{ndef}{NDEF}{NFC Data Exchange Format}
\newacronym{gcc}{GCC}{GNU Compiler Collection}
\newacronym{gdb}{GDB}{GNU Debugger}
\newacronym{i2c}{I2C}{Inter-Integrated Circuit}
\newacronym{iic}{IIC}{Inter-Integrated Circuit}
\newacronym{spi}{SPI}{Serial Peripheral Interface}
\newacronym{usb}{USB}{Universal Serial Bus}
\newacronym{ufw}{ufw}{Uncomplicated Firewall}
\newacronym{pkg}{PKG}{Package}
\newacronym{ai}{AI}{Artificial Intelligence}
\newacronym{fdm}{FDM}{Fused Deposition Modeling}
\newacronym{sla}{SLA}{Stereolithography}
\newacronym{pla}{PLA}{Polylactic Acid}
\newacronym{abs}{ABS}{Acrylonitril-Butadien-Styrol-Copolymer}
\newacronym{tcp}{TCP}{Transmission Control Protocol}
\newacronym{udp}{UDP}{User Datagram Protocol}
\newacronym{stl}{STL}{Standard Triangle Language}
\newacronym{pcb}{PCB}{Printed Cirtcuit Board}
\newacronym{lan}{LAN}{Local Area Network}
\newacronym{wlan}{WLAN}{Wireless Local Area Network}
\newacronym{wan}{WAN}{Wild Area Network}
\newacronym{dc}{DC}{Direct Current}
\newacronym{ac}{AC}{Alternating Current}
\newacronym{iso}{ISO}{Internation Organisation for Standardization}
\newacronym{din}{din}{Deutsches Institut für Normung}
\newacronym{gpl}{GPL}{General Public License}
\newacronym{ble}{BLE}{Bluetooth Low Energy}
\newacronym{uci}{UCI}{Universal Chess Interface}
\newacronym{fen}{FEN}{Forsyth-Edwards-Notation}
\newacronym{xfen}{X-FEN}{Extended Forsyth-Edwards-Notation}
\newacronym{ajax}{AJAX}{Asynchronous JavaScript and XML}
\newacronym{hal}{HAL}{Hardware Abstraction Layer}
\newacronym{fifo}{FIFO}{First In – First Out}
\newacronym{json}{JSON}{JavaScript Object Notation}
\newacronym{led}{LED}{Light-Emitting Diode}
\newacronym{pwm}{PWM}{Pulse Width Modulation}
\newacronym{gpio}{GPIO}{General Purpose Input/Output}
\newacronym{id}{ID}{Identifikator}
\newacronym{cnc}{CNC}{Computerized Numerical Control}
\newacronym{tls}{TLS}{Transport Layer Security}
\newacronym{ssl}{SSL}{Secure Sockets Layer}
\newacronym{dhcp}{DHCP}{Dynamic Host Configuration Protocol}
\newacronym{udev}{UDEV}{userspace device file system}
\newacronym{hf}{HF}{high frequency}
\newacronym{uscf}{USCF}{United States Chess Federation}
\newacronym{dsi}{DSI}{Display Serial Interface}
\newacronym{hdmi}{HDMI}{High Definition Multimedia Interface}
\newacronym{gpu}{GPU}{Graphics Processing Unit}
\newacronym{cpu}{CPU}{Central Processing Unit}

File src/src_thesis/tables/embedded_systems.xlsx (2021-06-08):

 | Raspberry-Pi 3b+ | STM32MP157A-DK1
Prozessor | Arm Cortex-A53 | Arm Cortex A7 + Arm Cortex A4
Arbeitsspeicher | 1GB LPDDR2 SDRAM | 4-Gbit DDR3L
Flash-Speicher | SD-Karte | SD-Karte
(+gpio)-Header | ja (40 Pol, (+i2c),(+spi)) | ja (40 Pol, (+i2c),(+spi))
Netzwerkanschluss | (+lan), (+wlan) | (+lan), (+wlan)
Besonderheiten | 64-bit Prozessor | Arm Cortex A4 Co-Prozessor, Secure-Boot, Debugger
Disable Motors | M84 | X Y

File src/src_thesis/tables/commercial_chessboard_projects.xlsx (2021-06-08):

 | Square Off – Kingdom | Square Off - Grand Kingdom | DGT Smart Board | DGT Bluetooth Wenige
Erkennung Schachfigurstellung | nein (Manuell per Ausgangsposition) | nein (Manuell per Ausgangsposition) | ja (Resonanzspulen) | ja((+rfid))
Abmessungen (LxBxH) | 486mm x 486mm x 75mm | 671mm x 486mm x 75mm | 540mm x 540mm x 20mm | 540mm x 540mm x 20mm
Konnektivität | (+ble) | (+ble) | (+usb) / Seriell | Bluetooth 2.0
Automatisches Bewegen der Figuren | ja | ja | nein | nein
Spiel Livestream | ja | ja | ja | ja((+rfid))
Cloud anbindung (online Spiele) | ja (über Mobiltelefon + App) | ja (über Mobiltelefon + App) | ja (über PC + App) | ja (über PC + App)
Parkposition für ausgeschiedene Figuren | nein | ja | nein | nein
Stand-Alone Funktionalität | nein (Mobiltelefon erforderlich) | nein (Mobiltelefon erforderlich) | nein (PC erforderlich) | nein (PC erforderlich)
Besonderheiten | Akku für 30 Spiele | Akku für 15 Spiele | Bussystem | -

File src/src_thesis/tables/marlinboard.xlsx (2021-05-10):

 | SKR 1.4 Turbo | Ramps 1.4 | Anet A8 Mainboard
Stepper Driver | TMC2209 | A4988 / TMC2209 | A4988
LED Strip Port | WS2811 / RGB | - | -
Firmware | Marlin-FW 2.0 | Marlin-FW 1.0 | proprietary

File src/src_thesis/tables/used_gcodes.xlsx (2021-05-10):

 | G-Code Command | Parameters
Move X Y | G0 | X<dest_pos_x_mm> Y<dest_pos_y_mm>
Move Home Position | G28
Set Units to Millimeters | G21
Set Servo Position | M280 | P<servo_index> S<servo_position>
Disable Motors | M84 | X Y

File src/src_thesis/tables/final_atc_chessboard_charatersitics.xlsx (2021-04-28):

 | Atomic Chess – autonomous Chessboard
Erkennung Schachfigurstellung | ja
Feldabmessungen (LxBxH) | 57x57mm
Abmessungen (LxBxH) | 620x620x170mm
Gewicht | 5.7kg
Konnektivität | (+wifi), (+usb)
Automatisches Bewegen der Figuren | ja
Spiel Livestream | ja
Cloud anbindung (online Spiele) | ja
Parkposition für ausgeschiedene Figuren | ja
Stand-Alone Funktionalität | ja

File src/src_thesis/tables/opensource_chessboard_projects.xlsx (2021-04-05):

 | Automated Chess Board (Michael Guerero) [@actproject1] | Automated Chess Board (Akash Ravichandran) [@actproject2] | DIY Super Smart Chessboard [@actproject3]
Erkennung Schachfigurstellung | nein (Manuell per Ausgangsposition) | ja (Kamera / OpenCV) | nein
Abmessungen (LxBxH) | keine Angabe | keine | 450mm x 300mm x 50mm
Konnektivität | (+usb) / Seriell | Ethernet, (+wlan) | Ethernet, (+wlan)
Automatisches Bewegen der Figuren | ja | ja | nein
Spiel Livestream | nein | nein | nein
Cloud anbindung (online Spiele) | nein | nein | ja
Parkposition für ausgeschiedene Figuren | nein | nein | nein
Stand-Alone Funktionalität | nein (PC erfoderlich) | ja | ja
Licence | (+gpl) 3+ | (+gpl) | -
Besonderheiten | - | Sprachsteuerung (Amazon Alexa) | Zuganzeige über LED Matrix

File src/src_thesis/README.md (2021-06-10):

# AtomicChessThesis

Das eigentliche Dokument ist die `thesis_document.md`. Die finale PDF `thesis.pdf` ist soweit aktuell, wenn ich diese erstelle, dies ist hier im Repo noch nicht automatisiert.
Ein bauen per Dockerimage ist möglich mittels ` build_thesis_docker.sh` Script und erzeugt die `thesis.pdf` neu.

# CHANGELOG

# 10.06.2021

* final spelling, " ", code korrektur/check
*

# 08.06.2021

* 4.2 - Auswahl des eingebetteten Systems (neu)
* Tabellen Fix (neu) für Tabelle 2.1 und Tabelle 2.2

# 07.06.2021

* einarbeitung Kommentare (neu)

# 05.06.2021

* 7.3 Service: Backend - Matchmaking+Beispiel (bearbeitet)
* 7.3 Service: Backend - Docker-Compose Code (bearbeitet)

# 04.06.2021

* Abstract - thesis_abstract.md (neu)
* 9.0 Anhang entfernt (neu)

# 02.06.2021

* einarbeitung Kommentare (neu)
* 4.0 Machbarkeitsanalyse und Verifikation ausgewählter Technologien (neu)

# 31.05.2021

* anpassungen Bilder (überarbeitet)
* abstract (neu)
* Zusammenfassung Kapitel 4 +5 => Machbarkeitsanalyse und Verifikation ausgewählter Technologien
* 4 Machbarkeitsanalyse und Verifikation ausgewählter Technologien (neu)
* 4.1 ErprobungBuildroot-Framework (neu)
* 4.2 Verifikation NFC Technologie (neu)
* 4.3 Schrittmotor/Schrittmotorsteuerung (neu)
* 8.0 Embedded System Software (neu)

# 30.05.2021

* 10 - Fazit (neu)
* 10.1 - persoenliches Fazit (neu)
* 10.2 - Ausblick (neu)

# 28.05.2021

* 8.2 - Service Architektur (neu)
* added Haskel to Dockerfile
* added csv2table pandoc filter
* added bib ref for docker, redis, mongo, docker-compose

# 27.05.2021 

* anpassungen Bilder (überarbeitet)

# 26.05.2021 II

* 8.4 - Backend (neu)

## 26.05.2021 I

* 1.1 - Motivation (überarbeitet)
* 6.1 - Mechanik (Bild eingefügt)
* 7.2 - Optimierungen der Spielfiguren (Bild eingefügt)
* 7.5 - Fazit bezüglich des finalen Prototypens (neu)

## 25.05.2021 II

* einarbeitung Kommentare 11:49
* einfügen Referenzen für Tabellen

## 25.05.2021 I

* 6.5 - Fazit des ersten Prototypens
* 7.1.1 - Gehäuse und Design
* 7.1.2 - 3D-Komponenten
* 7.1.3 Positions-Mechanik
* 9.1 - Ablaufdiagramm
* 9.2 - Figur Bewegungspfadberechnung

## 24.05.2021

* 6.3 - Schaltungsentwurf
* 6.4 - Implementierung HAL
* 7.1 - Modifikation der Mechanik

## 23.05.2021

* pandoc chapter numbering fix
* delaration, abstract toc fix
* pcb, schematic img added

## 21.05.2021 - INITIALE VERSION

* 3 - Einleitung, Motivation, Methodik
* 4.1 - 4.3, Analyse
* 5.4 - 3D Druck
* 6.1 - 6.2, Mechanik
* 7.2 - 7.3 - Optimierungen HWRev 2, HAL
* 8.5 - 8.7 - AutoPlayer WebClient
* 9.3 - 9.4 IPC User-Interface

## BUILD THESIS thesis_document

`$ bash ./build_thesis_docker.sh`

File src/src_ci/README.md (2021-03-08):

## Continous Integration

### WHY CI

### ADVANTAGES IN THIS PROJECT

For debugging and testing, building, checking the result, doing these step manually is okay.
But after the basic setup is working, the next task is to automate this tasks.
Especially, becuase the build process of buildroot can take serveral hours and the development pc is working hard to accomplish this task.
A good solution is outsource this task to a dedicated server. With an installed CI system on the server its not nessessary to kick off the process manualy.

The end result should be:

* Developer commits changes to release branch
* CI System detect changes and starts build process
* After successful build, save build artefacts
* (Publish build artefacts to production system)

In the case of building an sd card image for the embedded system, a manual step is needed to get the build files from the CI system running. So the CI can not publish the artefact to a production system. A better solution in this task is, to notify the developer that a build is succeed.

In this chapter we are getting to setup the jenkins software and create a configuration for the buildroot project in order to build the images for the embedded system automaticly.

### WHAT IS JENKINS

### SETUP JENKINS BLUEOCEAN

For this setup, the server is a virtual machine hosted on AWS (Amazon Web Service). Here is used a `AWS EC2 t3.2xlarge` instance.
This instance type offers 8 cpu threads and 32GiB of RAM. The Harddrive-Storage is here not important, the network troughput too.
As virtual machine base image (OS), we choose Amazon Linux which is based on Debian Linux.
It has a basic setup and ships with preinstalled applications like Docker, it is also hardened about remote root access.

This virtual machine is used to host the Jenkins Master, Build-Agents and the ATC_Server.

#### INSTALL JENKINS BLUEOCEAN

The setup of the jenkins software is very easy though the usage of Docker.
Jenkins offers a Docker-Image which can be installed though the `docker-cli`:

* `$ docker --version`, checks if docker is installed.
* `$ docker container run --name jenkins-blueocean --network host --env DOCKER_HOST=tcp://docker:2376 -v $(pwd)/jenkins_conf:/var/jenkins_home -p 8080:8080 -p 50000:50000 --restart always jenkinsci/blueocean`, pull docker image and start a new container using this image.

##### SITENOTE CONTAINER MANAGEMENT

Its possible to manage all docker container thought the `docker-cli`. There is also a webinterface for manage them, called portainer.
The portainer-webinterface allows to start/stop/create containers, image repository management and gives detailed logs and statistics over running containers.
Portainer is also able to manage a docker swarm or stack environment. In this reason portainer was also used to manage the docker environment on the remote server from the development pc.

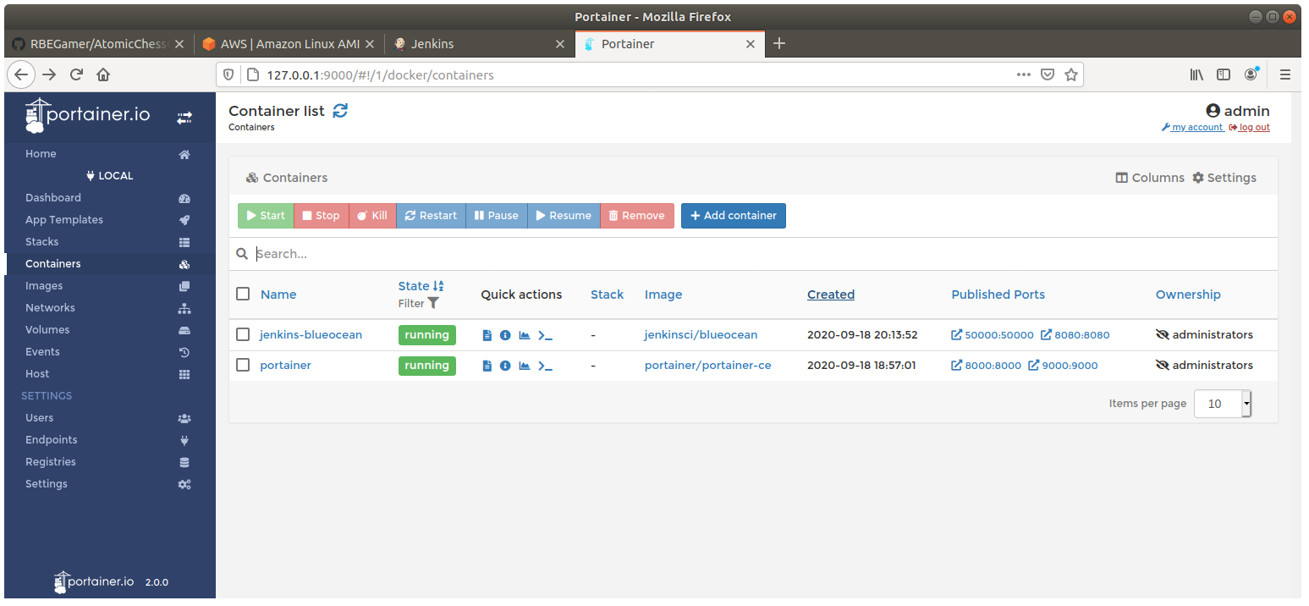
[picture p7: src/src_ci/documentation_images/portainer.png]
PORTAINER


The installation of portainer is very simple:

* `$ docker volume create portainer_data`, creates a volume for configuration data.
* `$ docker run -d -p 8000:8000 -p 9000:9000 --name=portainer --restart=always -v /var/run/docker.sock:/var/run/docker.sock -v portainer_data:/data portainer/portainer-ce`, start the portainer container. Its important to mount the local docker environment to the container using `-v /var/run/docker.sock:/var/run/docker.sock`.

The webinterface can be accessed with an brower pointing to `http://127.0.0.1:9000/`.

##### END SITENOTE

The Container needs two ports to be opened to the outside. On port `8080` the webinterface that jenkins provide can be accessed.
After successful start og the container, its possible to access the webinterface with the browser `http://127.0.0.1:8080/`.

The next steps are some basic installation questions:

* Install recommended plugins
* Setup a user account

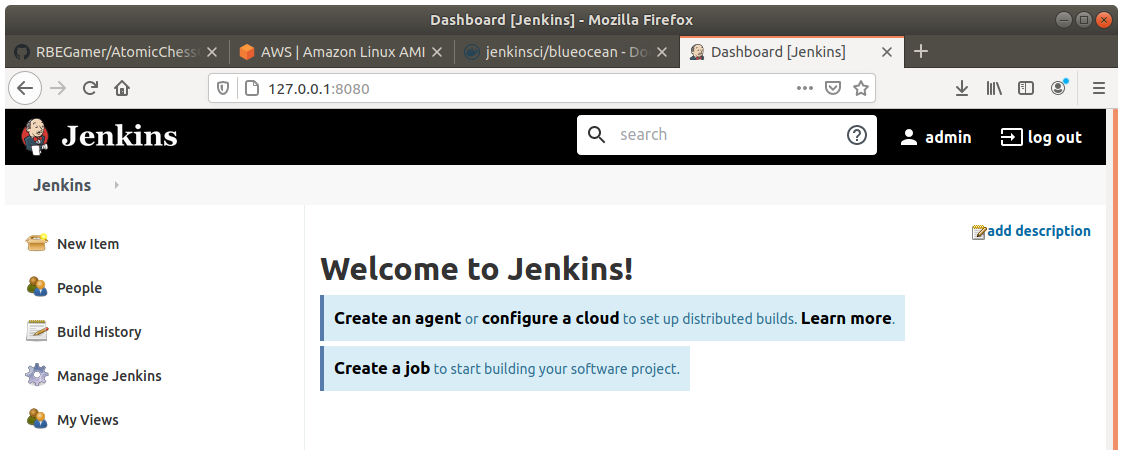
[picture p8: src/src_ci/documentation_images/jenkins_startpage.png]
JENKINS_STARTPAGE


Now we need to setup a few things in Jenkins before creating a new Job.

#### CREATE SSH CREDENTAILS

The sourcecode of the buildroot project, is stored in a git repository.
The repository is private and a clone is only possible, if the ssh key of the git client is registered on the git server.

On the development pc this is already the case, because it is needed to pull and push changes to the git repository.

On the Jenkins site, is is also nessessary, otherwise the jenkins agent can not pull the sourcecode from the git repository.

For security resonse the first step is to generate a new ssh keypair, that is only used for the jenkins<->git authentication.

A new keypair can generated with the `ssh-keygen` utility, which is installed on Ubuntu/Debian by default.

 `$ ssh-keygen -t rsa -C "jenkinsdev@prodevmo.com"`

 The tool asks for the storage location of the new key, here it is important to change the location due to avoiding to override existing keys.
 In the example the path `/home/prodevmo/.ssh/jenkins_master` was used.

 After `ssh-keygen` finished, it generates two files in the chosen directory:

 * `jenkins_master`, the private key file
 * `jenkins_master.pub`, the public key file

The content of the `jenkins_master.pub`, has to be saved on the git server.
For example, the process to add the new generated key to github is:

 Open a new brower and navigate to `github.com/settings/keys` and klick `new key`.
 In the following window paste the content of the `jenkins_master.pub` file and click `Add SSH Key`

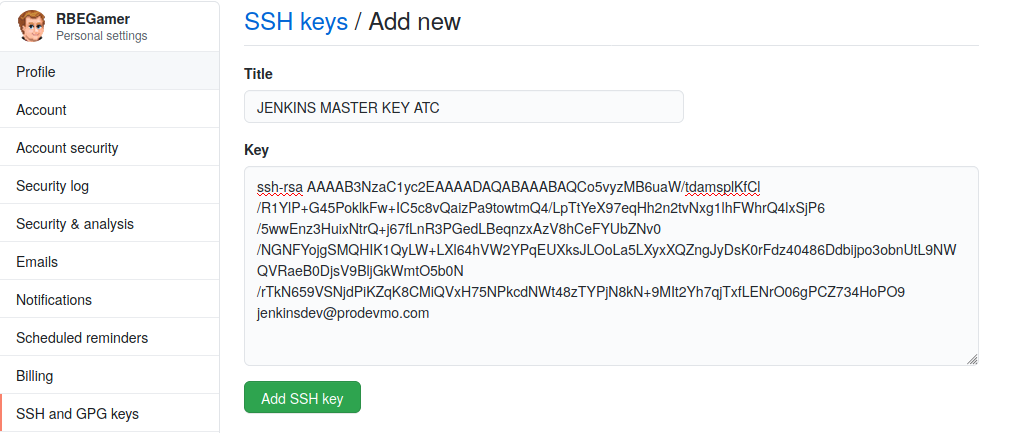
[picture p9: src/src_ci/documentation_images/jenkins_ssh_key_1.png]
JENKINS_SSH_PUB_KEY
 

 This proces is the same for other git systems like Bitbucket or GitLab, the GitHub workflow is only an example.

 Now the git server is setup with the new key, now we have to register the private key to the jenkins master.

 In order to do that, we have to navigate to the credentaials settings in jenkins : 
 `Jenkins->Manage Jenkins -> Manage Credentaials` and click under `Stores scoped to Jenkins` on `Domains (global)`.

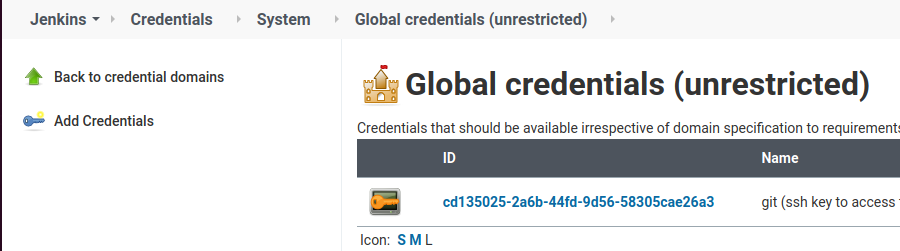
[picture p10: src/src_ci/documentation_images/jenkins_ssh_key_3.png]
JENKINS_SSH_JENKINS_SETUP


On the left window, click on `Add Credentials`, to add a new Entry.
Select in the `Kind` drop-down menu `SSH Username with private key`, and paste the content of the private key file `jenkins_master` into the textfield. After clicking on the `OK` Button the key is saved and the setup of the ssh key is complete.

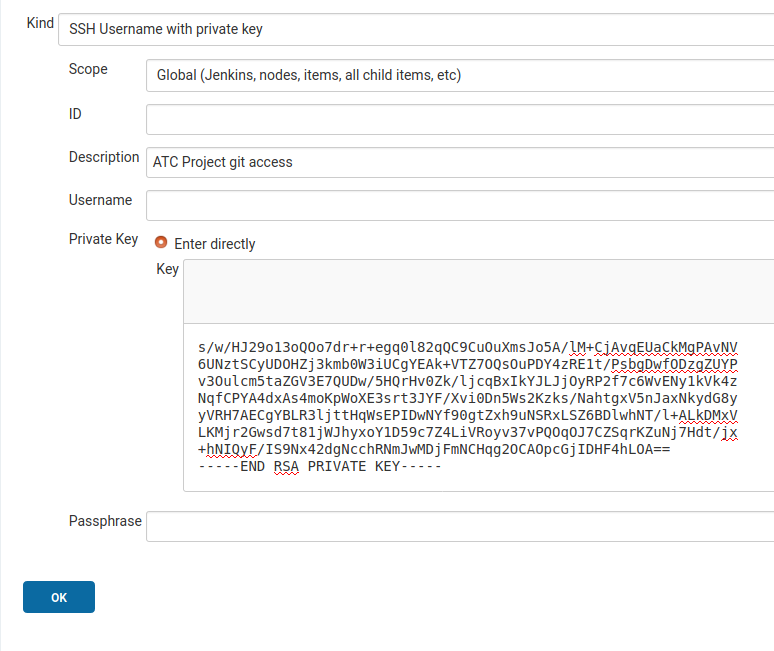
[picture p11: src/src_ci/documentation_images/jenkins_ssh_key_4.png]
JENKINS_SSH_JENKINS_SETUP_FINISHED


#### CREATE AGENT

##### SITENOTE SYSTEM REQUIREMENTS

Its possible to check if java version > 8 is on the system installed.

`$ java -version`

Otherwise it can be installed, using the apt package manager (Ubuntu/Debian).

`$ sudo apt install openjdk-14-jdk -y`

##### END SITENOTE
Before we can create a new job or project, its nessessary to create a build agent.
At this point we can only create one permanent agent. So the setup process is easy, simply clock thought the setup dialog.
In this installation, the name of the new agent is called `buildagent`.

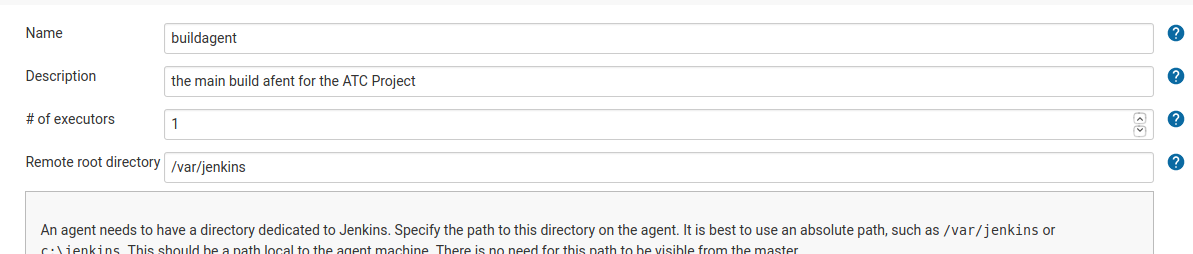
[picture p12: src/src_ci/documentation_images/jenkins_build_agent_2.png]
JENKINS_CREATE_AGENT


##### SITENOTE JENKINS VERSION >= 2.249.1
 In this version its is possible, that Jenkins can automaticly depoly and agent on a system. It uses a SSH connection into the system and setup and install a new agent. The process is very easy, its only nessessary to setup the ssh username/password or keyfile for the system with the jenkins credential manager. (See chapter CREATE SSH CREDENTAILS).

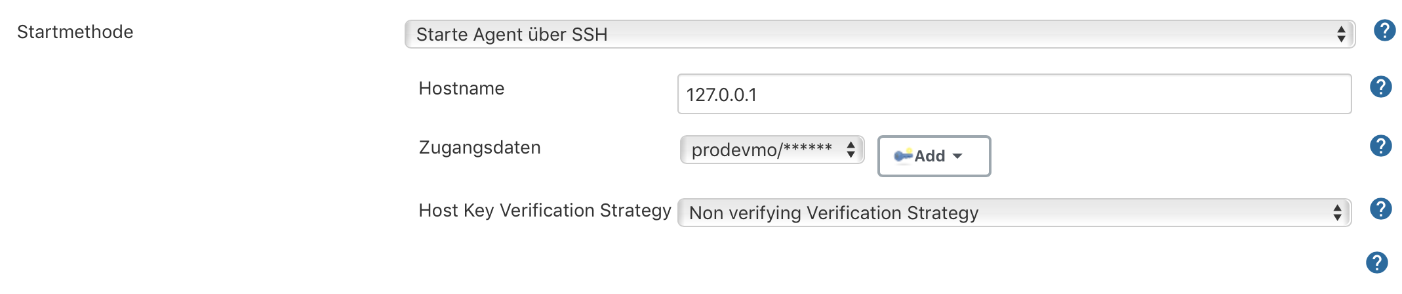
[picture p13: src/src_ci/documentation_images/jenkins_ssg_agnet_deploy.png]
JENKINS_CREATE_AGENT


The following steps, describes the tradiitional method for deploying a agent, using the downloaded agetn software and run it manually.
With the SSH deploy method, these steps can be skipped.

##### END SIDENOTE

On the jenkins agent overview page. Our new created agent is marked with a red cross symbol. This is becuase our created agent is not running on any system.
After a click on the agent `Jenkins->Nodes->buildagent` we can see on the status tab, a small manual how to start the agent.

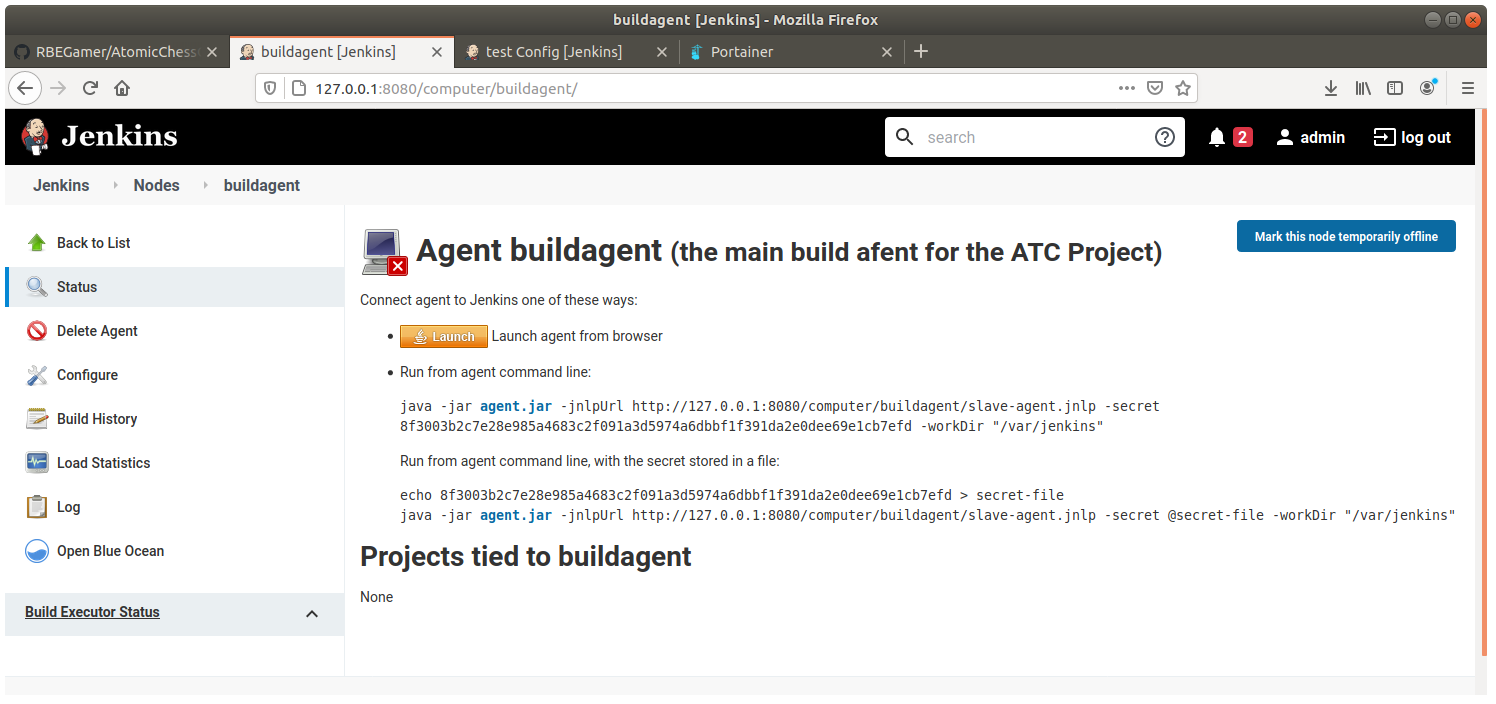
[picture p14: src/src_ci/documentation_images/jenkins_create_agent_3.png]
JENKINS_CREATE_AGENT


The agent can run on the same machine as the master or on any other system. In our case we start the agent on the same server as the jenkins container is running.

After downloading the `agent.jar` file and open the folder in a new terminal, we use the command given on the page to start the agent:
`$ java -jar agent.jar -jnlpUrl http://127.0.0.1:8080/computer/buildagent/slave-agent.jnlp -secret <SECRET_TOKEN> -workDir "/var/jenkins"`

After the agent is started, we can see on the status page, that the agent is connected and is waiting for jobs.

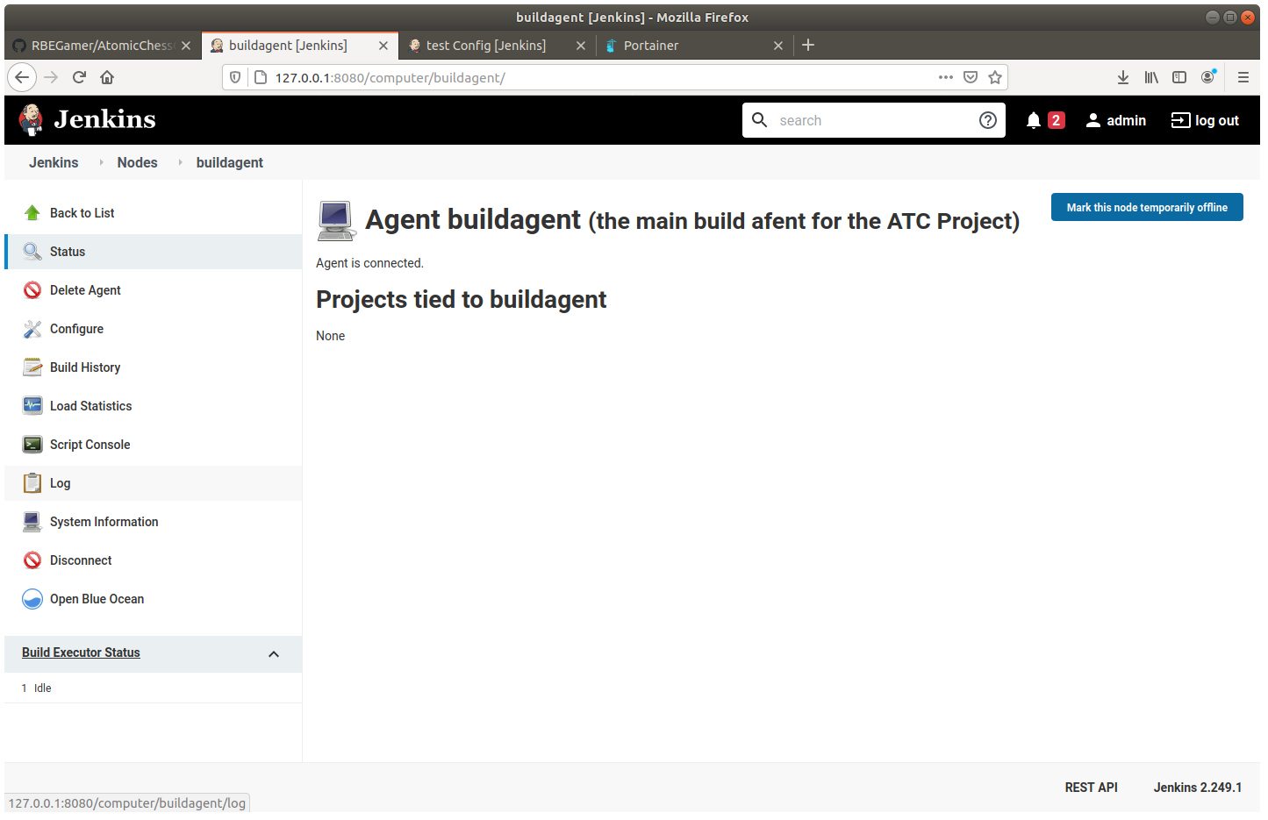
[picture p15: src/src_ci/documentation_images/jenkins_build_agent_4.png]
JENKINS_CREATE_AGENT


With this one agent installed, jenkins schedules any new build job to run on this agent.
Its also possible to give different agent different abilities. This can be used if a job has specific requirements to build.
For example the build process need specific hardware like a GPU or FPGA card or architecture, then its possible to run a agent on the specific hardware.
With labeling of the agent, its possible to tell jenkins that only jobs, that require special hardware to run on this agent.

For example the agent we setup before runs on a server with an Nvidia Tesla K80. In this case at setup, the agent was labaled with `CUDA_ENABLED`.
A job that requires CUDA can run on this agent.

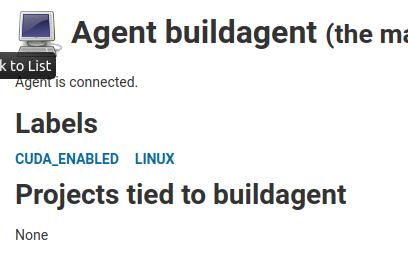
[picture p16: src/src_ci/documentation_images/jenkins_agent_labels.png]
JENKINS_AGENT_LABELS


##### NOTE
The system on which the new agent runs must have all the software installed to be able to build the software.
In the case of the buildroot project. A stock ubuntu installation already has all needed software packages installed.
For debian distributions the `build-essentaial` package is missing and an be installed using
`$ sudo apt install build-essential`.

#### CREATE JOB (PROJECT)

Now the basic jenkins setup is complete and the next step is to setup a project. Jenkins offers different kind of project templates.

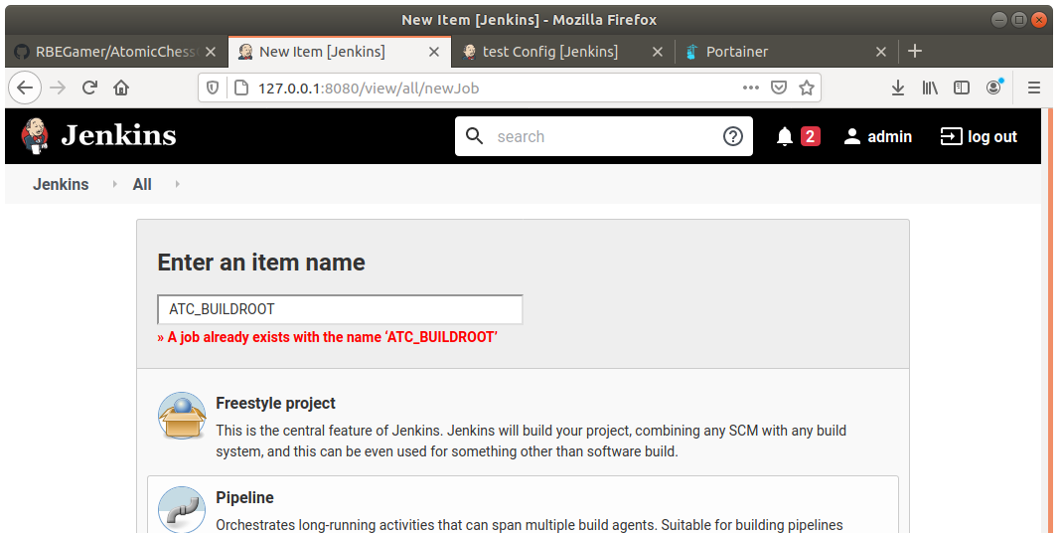
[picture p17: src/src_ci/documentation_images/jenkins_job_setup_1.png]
JENKINS_JOB_SETUP_1


For this simple job, to build our buildroot image, a `Freestyle project` was chosen.

The configuration page offers several different options for customizin the new project.
for this project we are only using a minimal subset of the possibilities jenkins offers.

##### Source Code Management

The first settings we have to change is the `Source Code Management` setting. The sourcecode of this project, is located in a git repository.
In order that jenkins find the sourcecode we have to make the following changes:

* `Git`
* `Repository URL`, the URL of the git repository.
* `Credentials`, select the SSH Credentials we have created earlier. 
* `Branches to build`, the branch to checkout. In our case the buildroot sourcecode is located in the `*/buildroot` branch.

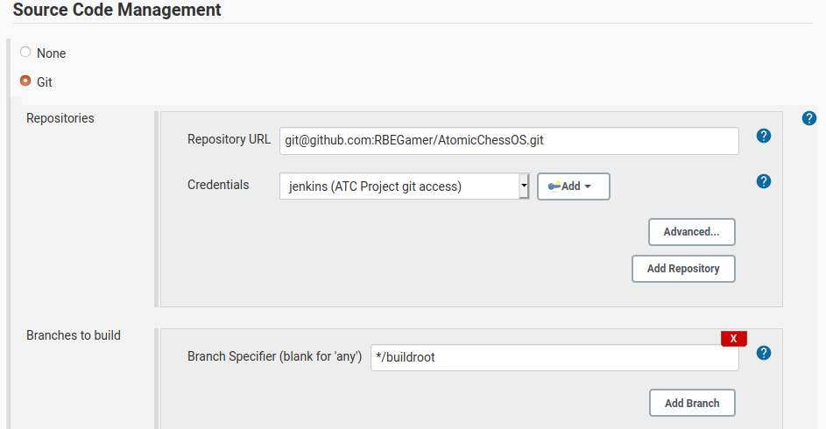
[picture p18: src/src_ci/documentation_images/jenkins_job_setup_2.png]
JENKINS_JOB_SETUP_SCM


##### Build Triggers

This options let us choose, when jenkins should start building the project.
There are several options, depensing on the type of project.
For example the option `Build after other project` is suitable, if the current project depends on an other projects build result.
With this option its also possible to setup a build pipeline.

* 1. build a library X
* 2. build the software based on this library X
* 3. deploy softwa to a production environment

The option `Build peridically` is a good option for long build tasks. Building the project always at the same time.
For example building a whole big project everyday at night, so the result is finished on the next day.

For this project, we want to build everytime a change was made in the git repository. Jenkins offer use two options for this

* `Webhook trigger`, gets notified from the git server about changes
* `Poll SCM`, poll the git repository every set timeinterval for changes

The `Webhook trigger` is the better solution for big repositories, because the `Poll SCM` method polls the complete repository in an interval, which cuases overhead.
The advantage of the `Poll SCM` method is that there is no setup required. Only the time interval for the polling has to be set.
In this project a interval of 5minutes was used.

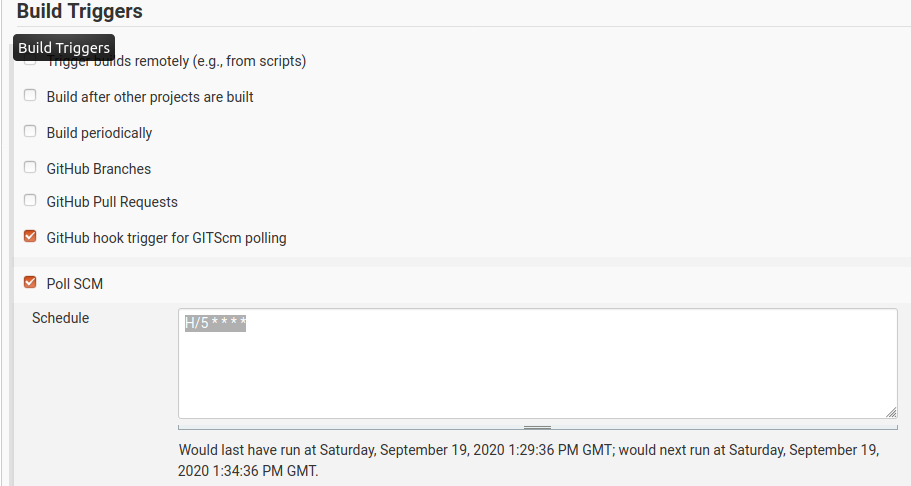
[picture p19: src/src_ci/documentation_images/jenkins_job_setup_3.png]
JENKINS_JOB_SETUP_SCM


##### Build Steps

###### BUILD
Now everythin is setup. Jenkins can pull the code from a git repository and detect changes automaticly in order to start a build.
The last thing missing are the steps that jenkins should execute in order to build.
These steps are called `build step`, and can be specified under the `Build` section.

To build the buildroot project, a filed called `build.sh` was created in the repository. So jenkins has simply to execute this file in a build step.

After clicking on the button `Add build step`, jenkins offers serveral different type of build steps.
To execute a bash file, the entry `Execute shell` is the right option.
In the following textbox, it is possible to write bash commands link in a `.sh` file.

The only line we need to sexecute the `build.sh` file is to navigate into the location of the file and execute these.

`$ cd ./src/src_buildroot/buildroot`
`$ ./build.sh`

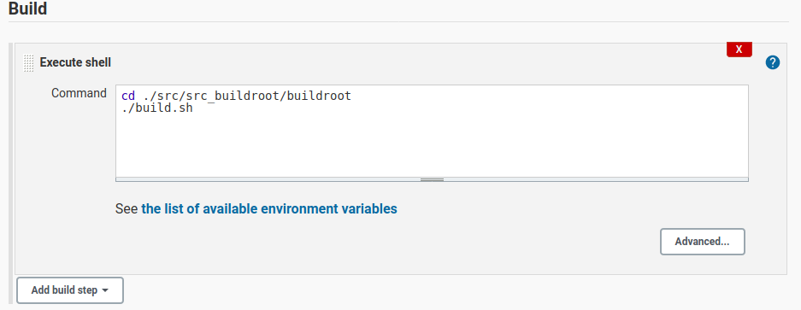
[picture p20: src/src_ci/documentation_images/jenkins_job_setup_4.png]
JENKINS_JOB_SETUP_SCM


###### POST-BUILD

Jenkins 

# HOW TO HANDLE ARTEFACTS
* what are artefacts
* using ftp to upload final image
* tag the git commit thats build

#### BUILD RESULT OVERVIEW

After successful setup of the job.
The last build status is shown on the job overview page.

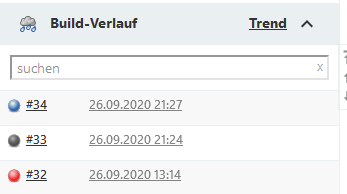
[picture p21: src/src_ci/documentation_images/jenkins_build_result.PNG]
JOB_STATUS


The blue dot indicated that the job was sucessful, a red dot that something failed.
By clicking on the job number, the complete job log output, runtime, artefacts are shown.

### CONCLUSION CONTINIOUS INTEGRATION WITH JENKINS

* easy setup with docker
* simple to use and setup
* perfect for long build tasks buildroot
* setup is usable for more project in the future

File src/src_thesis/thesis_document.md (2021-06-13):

# Einleitung

## Motivation

Eingebettete Systeme (Englisch "embedded Systems") sind technische Zusammensetzungen, die für eine spezifische Funktion entwickelt werden. Im Gegensatz zu Mehrzwecksystemen (Englisch "multi-purpose systems"), wie zum Beispiel einem Personal Computer, der in der Lage ist, diverse Funktionen auszuführen und nicht zwingend nur an eine Funktion gebunden ist, dienen eingebettete Systeme einer bestimmten Logik. Daraus resultieren einfachere und auch ressourcen-schonendere Systeme, die wesentlich näher an der Technik und der für den Zweck nötigen Komponenten und Software entwickelt werden. Systeme können günstiger zusammengesetzt und Fehlerquellen schneller entdeckt und behoben werden. Nicht für den Prozess notwendige Komponenten werden gar nicht erst verwendet. Bei einem Mehrzwecksystem wird akzeptiert, dass Komponenten und Schnittstellen existieren, die nicht benötigt werden. Diese verursachen Kosten und können mögliche Fehlerquellen sein.

<br>

Dennoch ist die Entwicklung eines solchen Systems nicht banal. Es ist abzuwägen, welche Komponenten derzeit auf dem freien Markt erhältlich sind, welche Eigenschaften diese mitbringen oder ermöglichen und wie diese optimal kombiniert werden können. Es bedarf im Vorhinein intensiver Recherche und einer größeren Perspektive über mögliche Zusammenhänge. 
Im Falle eines Mehrzwecksystems ist die Auswahl simpler, da man den Prozess auch im Nachhinein noch anpassen kann, zusätzliche Funktionen und Komponenten gegeben sind oder leichter ergänzt werden können. Das eingebettete System muss in der Regel aufgewertet oder sogar völlig ersetzt werden, wenn zu einem späteren Zeitpunkt festgestellt wird, dass Funktionen nicht gegeben oder umsetzbar sind. Fertige Systeme sind komplexer in der Aufwertung.

<br>

Die Fähigkeit zur Erstellung eines solchen Systems ist daher nicht als eine leichte Aufgabe anzunehmen und es ist mir wichtig, zum Abschluss meines Studiums mein gewonnenes Wissen über Systeme, Komponenten, Zusammenhänge und deren Verbindung bis hin zur Programmierung nachzuweisen. Die Auswahl eines fertigen Computers oder sogar das simple Nutzen existierender Betriebssysteme erweckt nicht den gleichen Reiz, wie es die eigene Erstellung dieser Komponenten auf mich hat. Ich halte es für essenziell, möglichst fachlich die Inhalte meines Studiums in Verbindung mit meinen Vorlieben zu bringen, um ein optimales Projekt zu erstellen.

<br>

Das dafür gewählte Projekt beinhaltet die Konstruktion und Automatisierung eines Schachtischs. Schach ist ein strategisches Brettspiel für gewöhnlich zwei Personen, bei welchem jeder Spieler 16 Figuren mit diversen Zug-Möglichkeiten nutzen kann, um den König des gegnerischen Spielers zu schlagen. Das Spiel basiert auf logischen Regeln und Spielverfahren, die bis hin zu komplexen Formationen und Bewegungen ausgebaut werden können. 

<br>

Die Erstellung eines autonomen Schachtischs vereinbart in meinen Augen im großen Umfang die wesentlichen Komponenten des Informatikstudiums mit meiner Vorliebe zur mechanisch-elektrischen Gestaltung. Angefangen mit den Grundlagen der Informatik, insbesondere mit technischem Bezug, über die Berechnung und Auslegung von Systemkomponenten, weiterhin die objektorientierte Projektplanung und Architektur von Systemen bis hin zu Datenbanken, Webtechnologien und Softwareentwicklung. Zudem wird mein Studienschwerpunkt, die technische Informatik, mit einem einbetteten System manifestiert. 

<br>

Schach ist ein bewährtes, ausnahmslos bekanntes und immer logisches Spiel, welches jedoch im kommerziellen Rahmen nie an Bedeutung gewonnen hat. Die Auswahl der verfügbaren elektrifizierten und programmgesteuerten Schachtische ist auffallend gering; zudem sind existierende Lösungen oftmals nicht erschwinglich und bedürfen erheblicher Anpassungen des Spielers an das Spiel.
Innerhalb der vergangenen drei Jahrzehnte bewiesen immer mehr Konzerne ihre technische Kompetenz und Überlegenheit und die Fähigkeit ihrer Maschinen mittels der Optimierung von Schachalgorithmen und dem möglichst schnellen Besiegen derzeitiger Schach-Meister und -Meisterinnen. Die Algorithmen stehen heute vielfach frei zugänglich zur Verfügung, jedoch ist das Interesse daran, für Spieler mögliche Anwendungen zu generieren, verschwindend gering und wird oftmals nur von Experten und Enthusiasten genutzt und auch erfragt. 

<br>

Mit dieser Arbeit möchte ich mich diesem Problem stellen und einen möglich günstigen Tisch entwickeln, welcher das Spielerlebnis ohne Einschränkungen dem Spieler transferiert. Zudem möchte ich gewonnene Erkenntnisse und aktuelle Ressourcen wie die Cloud-Infrastruktur einbinden, um das Schachspiel, welches normalerweise zweier Spieler bedarf, auch für einen einzelnen Spieler zu ermöglichen. Das Ergebnis soll nicht nur aus vielen Zeilen Code bestehen, sondern auch ein handfestes Produkt sein, das meine Qualitäten und meinen Enthusiasmus widerspiegelt. 

<br>

## Zielsetzung

Das Ziel der hier vorliegenden Arbeit ist es, einen autonomen Schachtisch zu entwickeln, der in der Lage ist, Schachfiguren selbstständig zu bewegen und auf Benutzerinteraktionen zu reagieren.
Darüber hinaus sollte der autonome Schachtisch weitere folgende Funktionalitäten aufweisen:

- Erkennung Figur-Stellung
- Automatisches Bewegen der Figuren
- Livestream des Spiels
- Parkposition für ausgeschiedene Figuren
- Stand-Alone Funktionalität 

<br>

Die Kernfrage der Arbeit bezieht sich somit auf die Überprüfung der Ausführbarkeit inklusive Erstellung und Umsetzung eines eingebetteten Systems und einer Cloud-Infrastruktur. 

<br>

Der Schwerpunkt liegt dabei insbesondere auf der Programmierung des eingebetteten Systems und dem Zusammenspiel von diesem mit einem aus dem Internet erreichbaren Server, welcher als Vermittlungsstelle zwischen verschiedenen Schachtischen und anderen Endgeräten dient.
Das Projekt umfasst zum einem die Positionserkennung und Steuerung der Hardwarekomponenten (Motoren, Sensoren) und zum anderen die Kommunikation zwischen dem Tisch selbst und einem in einer Cloud befindlichem Server.
Mittels der Programmierung werden diverse Technologien von verschiedenen Einzelsystemen zu einem Gesamtprodukt zusammengesetzt.
Insgesamt gilt es, einen für Anwender ansprechenden Schachtisch zu entwickeln, der das Spielerlebnis nicht nur originalgetreu widerspiegelt, sondern das Einzelspieler-Modell zusätzlich noch verbessert.

<br>

Der Grundgedanke dabei ist, dem Spieler die Arbeit des Versetzens der Spielfiguren und das Erwägen von gegnerischen Zügen abzunehmen. Somit ist ein komfortables Spiel auch gegen einen virtuellen Gegner möglich, das so bei einem Einzelspieler-Spiel das Überlegen und Ausführen von Spielzügen der Gegenseite entfällt.
Dem Spieler wird zudem die Möglichkeit geboten, gegen andere Spieler an diversen Orten oder gegen eine Schachlogik zu spielen und so Züge auszuführen, die jener im besten Fall nicht einmal vorhergesehen hat. Zudem wird die Korrektheit der getätigten Züge überprüft und sämtliche traditionellen Spielregeln in das Spiel miteinbezogen. Somit ist es nicht nur möglich, dass Anfänger das Spiel erlernen können, sondern auch bewährten Spielern mit unerwarteten Zügen des virtuellen oder realen Gegners neue Methodiken darzustellen.

<br>

Dies soll mittels eines kompakten und minimalistischem Designs realisiert werden. Darüber hinaus spielt nicht nur das Design eine Rolle, sondern auch die Handhabung. Dazu muss der Benutzer in der Lage sein, den Tisch in wenigen Handgriffen betriebsbereit zu machen und über eine einfach Bedienoberfläche eine neue Partie gegen den Computer oder einen anderen menschlichen Spieler zu beginnen. 

<br>

## Aufbau der Bachelorarbeit

Im zweiten Kapitel der hier vorliegenden Arbeit werden die zum Zeitpunkt des Projektstarts existierenden Produkte beziehungsweise öffentlich einsehbare Projekte und deren Umsetzung beleuchtet. Hier wird insbesondere darauf geachtet, die Grenzen bestehender Systeme darzulegen und nur die für dieses Projekt zutreffenden Funktionen zu vergleichen. 

<br>

Die Anforderungsanalyse im dritten Kapitel fasst alle zuvor recherchierten Funktionen bestehender Systeme zusammen und leitet daraus eine Auflistung der Anforderungen ab, welche in den nachfolgenden Prototypen realisiert werden sollen.
Hierbei wird darauf geachtet, dem Benutzer einen Mehrwert in Bezug auf die Benutzerfreundlichkeit und dem Umfang an Features zu bieten.

<br>

Nach der Festlegung der Anforderungen wird im vierten Kapitel eine Machbarkeitsanalyse durchgeführt.
In dieser wird untersucht, welche Technologien benötigt werden um, diese Anforderungen durch einen Prototyp erfüllen zu können.

<br>

Anschließend werden im fünften Kapitel die zuvor verwendeten Technologien betrachtet, welche bei den beiden darauffolgenden Prototypen verwendet wurden. Hierbei stehen insbesondere solche Technologien im Vordergrund der Untersuchung, welche möglichst einfach zu beschaffen sind und optimalerweise uneingeschränkt und lizenzunabhängig zur Verfügung stehen.

<br>

Das sechste Kapitel widmet sich der Realisierung eines ersten Prototyps dieses autonomen Schachtischs.
Hier werden die Erkenntnisse der zuvor evaluierten Technologien verwendet, um ein Modell zu entwickeln, welches den im ersten Abschnitt erarbeiteten Vorgaben entspricht. Der nach der Implementierung durchgeführte Dauertest soll zudem weitere Risiken, sowie mögliche Probleme und Fehlerquellen aufdecken.

<br>

Im anschließenden siebten Kapitel wird auf der Basis des ersten Prototypen und dessen im Betrieb verzeichneten Probleme der finale Prototyp entwickelt.

Hier werden die Schwierigkeiten durch die Vereinfachung der Elektronik sowie der Mechanik gelöst.
Die Zuverlässigkeit wurde mittels stetiger Testläufe mit kontrollierten Schachzug-Szenarien überwacht und so ein produktreifer Prototyp entwickelt.

<br>

Im darauffolgenden achten Kapitel wird die Cloud-Infrastruktur thematisiert, welche für eine Kommunikation zwischen den autonomen Schachtischen entscheidend ist.
Auch wird dabei die Software, welche auf dem eingebetteten System ausgeführt wird, im Detail beschrieben und deren Kommunikation mit der Cloud-Infrastruktur, sowie mit den elektrischen Komponenten beleuchtet.
Zusätzlich zu dieser system-internen Software wurde ein Webclient entwickelt, mit dem es Benutzern möglich ist, über einen Webbrowser gegen den Tisch zu spielen.
Dieser Client bot außerdem die Möglichkeit, das System schon im Laufe des Entwicklungsprozesses testen zu können.

<br>

Das neunte Kapitel beschreibt die Software, welche auf dem eingebetteten System ausgeführt wird.
Dessen Hauptaufgabe ist die Ansteuerung der Hardware-Komponenten, welche im autonomen Schachtisch verbaut sind.
Darunter zählt die Ansteuerung der Motoren um die Figuren autonom bewegen zu können und die Erkennung der vom Benutzer getätigten Schachzüge.
Das System befindet sich unterhalb des Spielbretts und übersetzt die von der Cloud-Infrastruktur abgefragten, über das Internet empfangenen Spieldaten in Spielzüge.
Dabei gilt ein besonderes Augenmerk der Berechnung der Figur-Bewegungen und dem Erkennen von durch den Benutzer getätigten Schachzügen.

<br>

Das zehnte und abschließende Kapitel umfasst das Fazit und gibt einen Ausblick auf mögliche Erweiterungen und Verbesserungen.

# Analyse bestehender Systeme

## Existierende Systeme im Vergleich

Im Folgenden werden vier kommerzielle und drei lizenzunabhängige (Open-Source) Schachtische miteinander verglichen.
Bei den ausgewählten Tischen handelt es sich um

- kommerziell
    - Square Off - Kingdom[@squareoffkingdom]
    - Square Off - Grand Kingdom[@squareoffgrand]
    - DGT Smartboard[@dtgsmartboard]
    - DGT Bluetooth Wenge[@dtgble] 
- open-source:
    - Automated Chessboard (Michael Guerero)[@actproject1]
    - Automated Chessboard (Akash Ravichandran)[@actproject2]
    - DIY Super Smart Chessboard[@actproject3]

<br>

Für die kommerziell käuflichen Schachtische und (intelligenten) Schachbretter \ref{commchesstables} gibt es kein sehr großes Marktangebot, weswegen für den Vergleich nur zwei Hersteller mit jeweils zwei verschiedenen Modellen gewählt werden konnten. Derzeit integriert nur eines dieser Unternehmen, `Square Off`, eine Funktion, welche die Figuren auf dem Tisch mittels einer Mechanik unterhalb der Tischplatte bewegen kann.

Der zweite Hersteller `DGT` wurde dennoch zum Vergleich von zusätzlichen Funktionen herangezogen, da dessen Schachbretter die aktuelle Figur-Stellungen erkennen können.
Die Tische des Herstellers `DGT` unterscheiden sich kaum in ihren Basis-Funktionen; mit steigendem Preis werden zusätzliche Funktionen in Form von Sensoren oder Verbindungsoptionen implementiert.

<br>

Das Angebot von open-source Schachtisch-Projekten \ref{oschesstables} hingegen ist breiter, jedoch sind die einzelnen Modelle oftmals Kopien oder Revisionen voneinander. Die möglichen Funktionen unterscheiden sich daher kaum. Für die hier dargestellte Übersicht wurden drei Modelle gewählt, welche in ihren Funktionen signifikante Auffälligkeiten und einen hohen Stellenwert und Bekanntheitsgrad aufweisen.
Wie bereits aus den zum Teil identischen Namen ersichtlich, streben alle Tische das gleiche Ziel an und unterscheiden sich daher nur geringfügig in ihren Funktionen, was im Folgenden nun näher erläutert wird.

<br>

### Kommerzielle Produkte

Die für den Vergleich gewählten Eigenschaften sind jene, welche die im Projekt angestrebten Funktionen möglichst äquivalent reflektieren. Dennoch schränkt das geringe Angebot an autonomen Tischen die Auswahl stark ein; daher wurde hierbei Wert gelegt auf Automation, Cloud-Anbindung und die Abmessungen, welche das Spielerlebnis am deutlichsten beeinflussen.

<br>

Die Bretter des Herstellers `DGT` erkennen die Position der verwendeten Figuren. Information über die dafür verwendete Technologie ist jedoch nicht verfügbar. Die `Square-Off`-Schachtische verfügen über keine solche Funktion.

<br>

Die Außenabmessungen der autonomen Schachtische unterscheiden sich nur beim Hersteller `Square Off` deutlich; 
der Grand Kingdom Schachtisch ist rechteckig konstruiert worden, was das Spielerlebnis deutlich verändert. Der simple Kingdom-Tisch ist dabei kleiner als das vorgegebene Turniermaß, was negativen Einfluss auf das Spielererlebnis hat. Mit den Standardmaßen der `DGT`-Spielbretter und zudem ihrer geringen Höhe gleichen diese deutlich einem Turniertisch. Die Kombination aus geringer Höhe und Erkennung der Figur-Stellung bei den `DGT`-Brettern ist positiv bemerkenswert. Die Größe der einzelnen Schachfelder aller autonomen Schachtische befinden sich jedoch in den Spezifikationen der (+uscf)[@officialuscfrules], welche sich von 50mm bis 63mm belaufen.

\pagebreak

: Auflistung kommerzieller autonomer Schachtische \label{commchesstables}

| | `Square Off` - Kingdom  | `Square Off` - Grand Kingdom | `DGT` Smart Board  | `DGT` Bluetooth Wenge |
|:---|---|:---:|:---:|---:|
| Erkennung Figur-Stellung | nein (manuell) | nein (manuell) | ja | ja |
| Abmessungen (LxBxH) | 486mm x 486mm x 75mm | 671mm x 486mm x 75mm | 540mm x 540mm x 20mm | 540mm x 540mm x 20mm |
| Konnektivität | Bluetooth | Bluetooth | Seriell | Bluetooth |
| Automatisches Bewegen der Figuren | ja | ja | nein | nein |
| Spiel Livestream | ja | ja | ja | ja |
| Cloud-Anbindung (online Spiele) | ja (App) | ja (App) | ja (PC + App) | ja (PC + App) |
| Parkposition für ausgeschiedene Figuren | nein | ja | nein | nein |
| Stand-Alone Funktionalität | nein (Mobiltelefon erforderlich) | nein (Mobiltelefon erforderlich) | nein (PC) | nein (PC) | 
| Besonderheiten | Akku für 30 Spiele | Akku für 15 Spiele | - | - |

\pagebreak

Beide Hersteller bieten eine Bluetooth-Schnittstelle an. Einzig das Smart-Board des Herstellers `DGT` nutzt eine serielle, kabelgebundene Schnittstelle.

<br>

Bei den `DGT`-Schachbrettern ist zu beachten, dass diese die Schachfiguren nicht autonom bewegen können. Sie wurden jedoch in die Liste aufgenommen, da sie einen Teil der Funktionalitäten der `Square Off` Schachbrettern abdecken und lediglich die automatische Bewegung der Schachfiguren fehlt.
Die `DGT`-Bretter können die Position der Figuren erkennen und ermöglichen so auch Spiele über das Internet; diese können sie auch als Livestream anbieten.
Bei Schachturnieren werden diese für die Übertragung der Partien sowie die Aufzeichnung der Spielzüge verwendet und bieten Support für den Anschluss von weiterer Peripherie wie zum Beispiel Schachuhren.

Somit gibt es zum Zeitpunkt der Recherche nur einen Hersteller von autonomen Schachbrettern, welcher auch die Figuren bewegen kann: `Square-Off`-Grand Kingdom bzw. `Square-Off`-Kingdom.

<br>

Ein Spiel-Livestream, d.h. eine Darstellung des aktuellen oder vergangener Spiele über eine Webanwendung, ist mit allen Tischen möglich. Da alle Tische eine Cloud-Anbindung besitzen, in der Regel mittels Applikation auf dem Smartphone oder Computer, wird lediglich des Versetzten von Figuren detektiert und in einer Oberfläche dargestellt.

<br>

Auffallend ist, dass nur einer der ausgewählten Tische über eine Parkposition für ausgeschiedene Figuren verfügt. Der `Square-Off`-Grand Kingdom, welcher Figuren automatisch verschieben kann, besitzt dank der rechteckigen Tischform die Möglichkeit, Figuren selbständig aus dem Spiel zu entfernen und bei Bedarf wieder ins Spiel zurückzuführen.

<br>

Ebenfalls erwähnenswert ist, dass keiner der Tische eine Stand-Alone-Funktionalität besitzt. Jeder Tisch benötigt eine Verbindung zu einem externen Gerät wie einem Smartphone oder Computer, welches dann die Berechnung der Gegnerzüge vornimmt. Keiner dieser Tische kann ein simples Spiel nach einem verbindungslosen Start ausführen.

Für die Schachtische der Firma `Square Off` ist eine Smartphone App `Square Off - Chess App`[@squareoffapp] für die Verwendung notwendig.
Die App wiederum fordert eine Registrierung inklusive Profilerstellung beim Hersteller. Erst danach ist ein Spiel gegen den Computer ohne Internet möglich.

<br>

Alle weiteren Optionen (wie bspw. Spiel gegen andere Spieler, Live-Stream) sind nur über einen Online-Zugang möglich und erfordern je nach gewählten Optionen auch einen weiteren Account bei anderen Schach-Cloud-Anbietern wie `Chess.com` oder `Lichess`.

<br>

Beide `Square-Off`-Modelle ermöglichen durch eingebaute Akkus auch eine mobile Nutzung, was dem Nutzer mehr Flexibilität, zum Beispiel das spielen im Freien, erlaubt.

<br>

Zusammenfassend ist festzustellen, dass alle vier Tische dank unterschiedlicher Ausführung von Spiel-Eigenschaften zu unterschiedlichen Spiel-Erlebnissen führen. Für Nutzer ist eine Entscheidung anhand von Funktionen kaum möglich; letztlich bedarf es vor einem Kauf der Auswertung von gewünschten und gegebenen Funktionen.

<br>

Es ist erkennbar, dass nur die Firma `Square Off` einen absolut autonomen Schachtisch anbietet, auch wenn dieser nicht alle in diesem Projekt angestrebten Funktionalitäten bietet. So hat der Nutzer im Hinblick auf kommerzielle Angebote kaum Auswahlmöglichkeiten.

<br>

### Open-Source Projekte

Bei allen Open-Source Projekten wurden die Eigenschaften anhand der Beschreibung und der aktuellen Software extrahiert \ref{oschesstables}.

<br>

Besonders bei Projekten, welche sich noch in der Entwicklung befinden, können sich die Eigenschaften noch verändern und so weitere Funktionalitäten hinzukommen.

<br>

Alle Eigenschaften der Projekte wurden zum Zeitpunkt der Recherche analysiert und dokumentiert und mit Beginn der Entwicklung als Struktur-Fixpunkt festgelegt. Nachfolgende Entwicklungen wurden nach diesem Zeitpunkt nicht mehr berücksichtigt.

<br>

Zusätzlich zu den genannten Projekten sind weitere derartige Projekte verfügbar; in der Tabelle wurde nur jene aufgelistet, welche sich von anderen Projekten in mindestens einem Feature unterschieden.

<br>

Auch existieren weitere Abwandlungen von autonomen Schachbrettern, bei welchen die Figuren von oberhalb des Spielbretts gegriffen bzw. bewegt werden. In einigen Projekten wird dies mittels eines Industrie-Roboters[@actprojectrobot] oder eines modifizierten 3D-Druckers[@atcproject3dprinter] realisiert. Diese wurden hier aufgrund der Mechanik, welche über dem Spielbrett montiert werden muss und damit das Spielerlebnis erheblich beeinflusst, nicht berücksichtigt.

<br>

In den bestehenden Projekten ist zu erkennen, dass ein autonomer Schachtisch sehr einfach und mit simplen Mittel konstruiert werden kann. Hierbei fehlen in der Regel einige Features, wie das automatische Erkennen von Figuren oder das Spielen über das Internet.
Einige Projekte setzten dabei auf eingebettete Systeme, welche direkt im Schachtisch montiert sind. Andere hingegen nutzen einen externen PC, welcher die Steuerbefehle an die Elektronik sendet.

<br>

Bei der Konstruktion der Mechanik und der Methode, mit welcher die Figuren über das Feld bewegt werden, ähneln sich jedoch die meisten dieser Projekte. Hier wurden in der Regel einfache X- und Y-Achsen verwendet, welche von je einem Schrittmotoren bewegt werden.
Die Schachfiguren werden dabei mittels eines Elektromagneten über die Oberseite gezogen. Dabei ist ein Magnet oder eine kleine Metallplatte als Gegenpol in den Fuß der Figuren eingelassen.

<br>

Die Erkennung der Schachfiguren ist augenscheinlich die schwierigste Aufgabe. Hier wurde in der Mehrzahl der Projekte eine Kamera im Zusammenspiel mit einer auf `OpenCV`-basierten Figur-Erkennung verwendet.
Diese Variante ist je nach Implementierung des Vision-Algorithmus fehleranfällig bei sich ändernden Lichtverhältnissen. Auch muss die Kamera oberhalb der Schachfiguren platziert werden, wenn kein transparentes Schachfeld verwendet werden soll.

Eine weitere Alternative ist die Verwendung einer Matrix aus Reed-Schaltern oder Halleffekt-Sensoren. Diese werden in einer 8x8 Matrix Konfiguration unterhalb der Platte montiert und reagieren auf die Magnete in den Figuren. So ist es möglich zu erkennen, welches der Schachfelder belegt ist, jedoch nicht konkret von welchem Figurentyp.
Dieses Problem wird durch eine definierte Ausgangsstellung beim Spielstart gelöst. Nach jedem Zug durch den Spieler und der dadurch resultierenden Änderungen in den Figurenpositionen in der Matrix können die neuen Figurenstellungen berechnet werden.

<br>

\pagebreak

: Auflistung von Open-Source Schachtisch Projekten \label{oschesstables}

| | Automated Chess Board (Michael Guerero) | Automated Chess Board (Akash Ravichandran) | DIY Super Smart Chessboard |
|:---|:---:|:---:|---:|
| Erkennung Figur-Stellung | nein (manuell) | ja (Kamera) | nein |
| Abmessungen (LxBxH) | keine Angabe | keine Angabe | 450mm x 300mm x 50mm |
| Konnektivität | (+usb) | (+wlan) | (+wlan) |
| Automatisches Bewegen der Figuren | ja | ja | nein |
| Spiel Livestream | nein | nein | nein |
| Cloud-Anbindung (online Spiele) | nein | nein | ja |
| Parkposition für ausgeschiedene Figuren | nein | nein | nein |
| Stand-Alone Funktionalität | nein (PC erforderlich) | ja | ja |
| Besonderheiten | - | Sprachsteuerung | Zuganzeige ((+led) Matrix) |
| Lizenz | (+gpl) 3+ | (+gpl) | - |

Abschließend ist festzuhalten, dass es auch bei den Open-Source Projekten kein Projekt gibt, welches alle gewünschten Features abbildet.
Auch fehlen dort weitestgehend Features, welche die kommerziellen Projekte bieten. Ebenso gilt dies für die kommerziellen Projekte, welche zwar viele Features bieten, jedoch dies zumeist in einem geschlossenen Ökosystem. Somit gibt es auch hier keinen klaren Testsieger, welche alle gewünschten Features abbildet.
Das Ziel der hier vorliegenden Arbeit soll nun sein, all die positiven Eigenschaften dieser Tische zu vereinigen und mittels noch zusätzlicher Verbesserungen ein eigenes Produkt zu entwickeln.

<br>

## User Experience

Ein wichtiger Aspekt bei diesem Projekt stellt die User-Experience dar. Diese beschreibt die Ergonomie der Mensch-Maschine-Interaktion und wird durch die `DIN 9241`[@din9241] beschrieben.
Darin geht es primär um das Erlebnis, welches der Benutzer beim Verwenden eines Produkts erlebt und welche Erwartungen der Benutzer an die Verwendung des Produkts hat.

<br>

Beim autonomen Schachtisch soll der Benutzer eine ähnlich authentische Erfahrung erleben wie bei einer Schachpartie mit einem menschlichen Gegenspieler.
Der Benutzer soll direkt nach dem Einschalten des Tisches und dem Aufstellen der Figuren in der Lage sein, mit dem Spiel beginnen zu können. Dies soll wie ein reguläres Schachspiel ablaufen; der Spieler vor dem Tisch soll die Figuren mit der Hand bewegen können und der Tisch soll den Gegenspieler darstellen.
Der Tisch soll somit die Figuren der Gegenseite bewegen.

<br>

Nach Beendigung einer Partie soll das Spielbrett wieder in die Ausgangssituation gebracht werden. Dies kann zum einem vom Tisch selbst oder vom Benutzer manuell geschehen.
Danach ist der Tisch für die nächste Partie bereit, welche der Benutzer einfach per Knopfdruck starten können sollte.

<br>

Dies soll auch für abgebrochene Spiele gelten, welche von Benutzer oder durch das System abgebrochen wurden. Auch in diesen Fällen soll das Schachbrett sich selbständig zurücksetzten können.

<br>

Ein weiterer Punkt, welcher bei der User-Experience beachtet werden soll, ist der zeitliche Aspekt. Ein Spiel auf einem normalen Schachspiel hat je nach Spielart kein Zeitlimit. Dies kann für das gesamte Spiel gelten oder auch für die Zeit zwischen einzelnen Zügen.
Der autonome Schachtisch soll es dem Spieler zum Beispiel ermöglichen, ein Spiel am Morgen zu beginnen und dieses erst am nächsten Tag fortzusetzen.

<br>

Auch muss die Frage beantwortet werden, was mit den ausgeschiedenen Figuren geschehen soll. Bei den autonomen Schachbrettern von `Square Off` werden die Figuren an die Seite auf vordefinierte Felder bewegt und können so bei der nächsten Partie vom System wieder aufgestellt werden. Viele andere Projekte schieben die Figuren aus dem Feld heraus, können diese aber im Anschluss nicht mehr gezielt in das Feld zurückholen. So muss diese Aufgabe vom Benutzer manuell durchgeführt werden. Von einigen Projekten wird die Behandlung ausgeschiedener Figuren gar nicht abgedeckt und der Benutzer muss die Figuren selbständig vom Feld entfernen.

<br>

# Anforderungsanalyse

Nach Abschluss der Recherche, kann somit eine Auflistung aller Features \ref{atcrequirements} angefertigt werden, welche ein autonomer Schachtisch aufweisen sollte.
In diesem Projekt werden vor allem Funktionalitäten berücksichtigt, welche bei Bedienung und Benutzung des autonomen Schachtisches dem Benutzer einen Mehrwert in Bezug auf die Benutzerfreundlichkeit bieten.

<br>

: Auflistung der Anforderungen an den autonomen Schachtisch \label{atcrequirements}

| | (+atc) |
|:--- |---:|
| Erkennung Figur-Stellung | ja |
| Konnektivität | (+wlan), (+usb) |
| Automatisches Bewegen der Figuren | ja |
| Spiel Livestream | ja |
| Cloudanbindung (online Spiele) | ja |
| Parkposition für ausgeschiedene Figuren | ja |
| Stand-Alone Funktionalität | ja (Bedienung direkt am Tisch) |

<br>

Die Abmessungen und das Gewicht des autonomen Schachtisches ergeben sich aus der mechanischen Umsetzung und werden hier aufgrund der zur Verfügung stehenden Materialen und Fertigungstechniken nicht festgelegt.
Dennoch wird Wert daraufgelegt, dass der Unterschied zwischen den Spielfeldabmessungen und den Abmessungen des Tisches so gering wie möglich ausfällt.

Auch müssen die Figuren für den Benutzer eine gut handhabbare Größe aufweisen, um ein angenehmes haptisches Spielerlebnis zu gewährleisten.
Diese richten sich hierbei an die Größe des Spielfeldes. Des Weiteren gibt es auch hier von der (+uscf)[@officialuscfrules] Spezifikationen über die Größe der Figuren, jedoch sollen diese hier nicht zwingend angewendet werden, da diese speziell für den autonomen Schachtisch angepasst werden müssen, um eine automatische Erkennung dieser durch den Schachtisch gewährleisten zu können.

Ebenfalls wird kein besonderer Augenmerk auf die Geschwindigkeit der Figur-Bewegung gelegt, solange dies nicht das Spielerlebnis stört. Die Zuverlässigkeit und Wiederholgenauigkeit dieser Bewegungen sollen dabei im Vordergrund stehen, um einen reibungslosen Spielablauf zu gewährleisten..

# Machbarkeitsanalyse und Verifikation ausgewählter Technologien

Da dieses Projekt aus vielen ineinandergreifenden Komponenten besteht wurden zuerst Technologien ausgewählt, welche sich augenscheinlich für die Umsetzung eignen.
Hier werden Technologien für die folgenden Komponenten benötigt:

- Erstellung von Software-Paketen für das eingebettete System
- Auswahl des eingebetteten Systems
- Identifizierung der Schachfiguren
- Mechanische Bewegung der Schachfiguren

## Erprobung Buildroot-Framework

Eine Hürde, welche bei diesem Projekt genommen werden musste, war die Erstellung der Software, welche auf dem autonomen Schachtisch ausgeführt wird.
Hierbei sollte diese nicht von Grund auf neu entwickelt werden, sondern auf einer soliden Basis aufbauen.
Allgemein soll hier auf ein minimales Linux-System gesetzt werden, in welches die Software des autonomen Schachtisch integriert wird. 
Auf dem Basis-System müssen die folgenden Software-Pakete installiert sein bzw. einfach integrierbar sein:

- (+ssh) für den Remote-Zugriff
- (+dhcp) Client zur automatischen IPv4-Adressvergabe
- (+udev) zur Ein-/Ausgabe Geräteverwaltung (Touchscreen)
- Qt[@qtframework] - (+gui) Framework
- SW-Update zur Durchführung von Remote-Software-Updates der Schachtisch-Software

Auf Seiten der Entwicklung war eine Toolchain notwendig, mit welcher es möglich sein sollte, in C++ geschriebene Programme auf dem System ausführen und mittels (+gdb) auf Fehler überprüfen zu können. Zusätzlich sollte der C++ Compiler mindestens den C++17 Standard unterstützen.

<br>

Zusätzlich zu diesen auf dem Linux-System benötigten Paketen sollte es möglich sein, ein durch das eingebettete System bootbares Dateisystemimage zu erzeugen.
Für diesen Zweck existieren einige Open-Source Projekte, welche solch ein Build-System bereitstellen. 

<br>
Hierbei existieren zwei weit verbreitete Systeme:
Das `Yocto`-Projekt[@yoctoproject] und das Buildroot[@buildrootproject]-Framework.
Diese unterscheiden sich im Aufbau und der Funktionsweise teils stark, vor allem während der ersten Verwendung.

<br>

: Vergleich Yocto - Buildroot \label{commchesstables}

| | `Yocto`-Project | `Buildroot`-Framework |
|--- |--- |--- |
| Dependency-Management | Nein | Ja |
|  Partielle Updates | Ja | Nein |
| Automatischer Paket-Download | Nein | Ja |
| Verwendung Build-Cache | Ja | Nein |
| Einfache Konfiguration | Nein | Ja |
| | | |

<br>

Hierbei stellt das `Yocto`- Projekt eine größere Einsteigshürde dar, aufgrund seines komplexen Layer-Systems.
Es bietet sich jedoch für komplexe Projekte an, welche einen hohen Grad an Individualisierung benötigen. Ein Nachteil dessen ist, dass dadurch vieles vom Nutzer selber konfiguriert werden muss, bevor ein minimales System in Betrieb genommen werden kann.

<br>

Somit muss zuerst eine grundlegende Konfiguration für das eingebettete System angelegt werden und es kann nicht direkt mit einem fertigen minimalen System mit der eigentlichen Software-Entwicklung gestartet werden. Allgemein sind die Anforderungen an die zu erstellende Software und deren benötigte Requirements sehr gering, sodass hier eine detaillierte Einarbeitung zeitlich nicht möglich war.

<br>

Der Aufbau dieser Konfiguration des `Yocto`- Projekt besteht aus drei Schichten:

- Layer - Build-Metadaten
- Recipes - Pakete
- Bitbake - Tool zum erstellen

Eigene Pakete werden dabei in `Recipes` angelegt, welche in einer Makefile ähnlichen Syntax das Paket und die Schritte zum erstellen beschreiben. Diese einzelnen Pakete werden anschließend in `Layern` zu einem Gesamtsystem zusammengesetzt. Dies geschieht anschließend mittels des `Bitbake`-Tools, welches das System erstellt.

<br>

Das `Buildroot`-Framework hingegen bietet bereits eine große Anzahl an vorkonfigurierten Ziel-Systemen an, für welche es bereits alle nötigen Parameter enthält, um ein minimales solches System erstellen zu können. Auch ist bereits eine optimierte Konfiguration für das im Rahmen des hier vorliegenden Projekts gewählte eingebettete System vorhanden, welche direkt gestartet werden kann.

<br>

Nach einem erfolgreichen Erstellen des Images kann dieses direkt über das eingebettete System gestartet werden.
Bei jedem Build-Vorgang müssen jedoch alle Pakete erneut gebaut werden, bevor diese zu einem finalen Image zusammengefügt werden.
Hierbei kann dieser Vorgang je nach Umfang der verwendeten Pakete mehrere Stunden dauern. Das `Yocot`-Projekt unterstützt hierbei das Erstellen einzelner Pakete, somit müssen nur Änderungen neu gebaut werden.
Da im Rahmen dieses Projekts nur eine minimale Anzahl von Paketen benötigt werden, hält sich dieser Buildvorgang zeitlich in Grenzen und ist allgemein für dieses Projekt nicht entscheidend.

<br>

Dann wurde prototypisch evaluiert, wie aufwändig es ist, zum `Buildroot` Framework eigene in C++ geschriebene Software hinzuzufügen.
Zu diesem Zweck wurde ein eigenes C++ Paket erstellt und in das `Buildroot`-Framework integriert. Hierzu wurden dem `Buildroot` Quellcode zwei weitere Dateien hinzugefügt.

Die `Config.in` beschreibt das Paket und legt Abhängigkeiten zu anderen Paketen fest.

```yaml
#atctp - Config.in - Package Configuration
config BR2_PACKAGE_ATCTP
    bool "ATC_TEST_PACKAGE"
    help
        This package is a test package to verify the buildroot build process
```

Die zweite Datei ist die `PAKET_NAME.mk - Makefile`, welche die Schritte beschreibt, welche zum Erstellen und Installieren des Paketes durchgeführt werden müssen. 

```yaml
# atctp - atctp.mk - Makefile
ATCTP_VERSION = 1.0.5
ATCTP_SITE = ./package/atctp/src
ATCTP_SITE_METHOD = local
ATCTP_LICENSE = GPL-2.0+

define ATCTP_BUILD_CMDS
    @echo ATCTP_BUILD!
    @echo $(@D)
    @echo -----------------
    $(MAKE) $(TARGET_CONFIGURE_OPTS) -C $(@D)
endef

define ATCTP_INSTALL_TARGET_CMDS
    @echo ATCTP_INSTALL!
    $(INSTALL) -D -m 0755 $(@D)/atc_testpackage $(TARGET_DIR)/usr/ATC/atc_testpackage
endef

$(eval $(generic-package))
```

Das somit erstellte Test-Paket `atctp` bildete eine funktionierende Grundlage für das System. Somit eignet sich das `Buildroot`-Framework optimal für dieses Projekt, da hier der Prozess zur Integration von eigener Software sehr einfach gestaltet ist.

<br>

## Auswahl des eingebetteten Systems

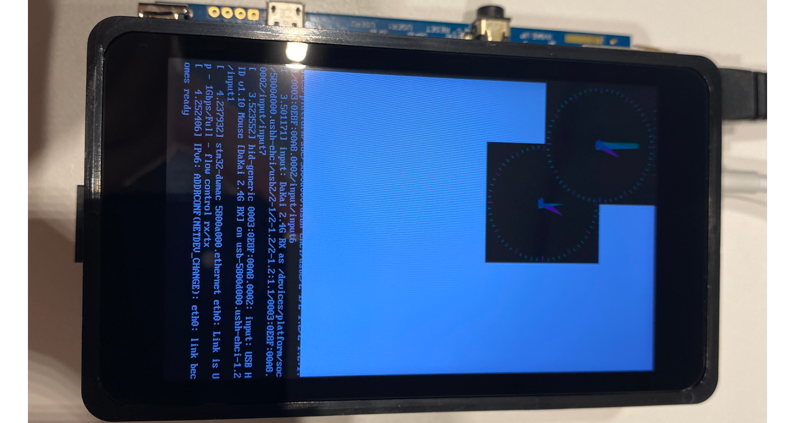
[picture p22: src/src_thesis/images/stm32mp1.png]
STM32MP1-DK2 \label{stm32mp1}


Zur Ansteuerung aller elektrischen Komponenten, welche den autonomen Schachtisch antreiben, wird ein eingebettetes System benötigt, auf welchem die zur vor erstellte Software ausgeführt wird.
Dies ist in diesem Fall, ein durch das `Buildroot`-Framework generierte Linux-Image.

<br>

Um mit den elektrischen Komponenten kommunizieren zu können, werden zusätzlich verschiedene Ein- und Ausgabe-Schnittstellen benötigt:

- (+hdmi) oder (+dsi)
- (+usb)
- (+gpio) Header mit (+spi) / (+i2c)-Bus
- (+lan) oder (+wlan)

Da es sich hier um einen Prototyp handelt und die finalen Anforderungen der Software und Hardware noch nicht final feststehen, sollte das eingebettete System genug Spielraum bieten, um spätere Erweiterungen umsetzten zu können.

<br>

Auch spielte bei der Auswahl die Verfügbarkeit zum Zeitpunkt der Evaluation eine Rolle, da hier einige andere Systeme unter anderem lange Lieferzeiten aufwiesen. Zudem wurde darauf geachtet, dass das System bereits in einigen anderen Projekten verwendet wird, sodass bei möglichen Problemen, Ressourcen für die Fehlerbehebung bereitstehen.

<br>

Somit beschränkte sich die Auswahl für diesen Prototyp, angesichts des für die Evaluation abgesteckten zeitlichen Rahmen auf den `Raspberry-Pi 3b+` und das `STM32MP157A-DK1`\label{ref}.

: Getestete eingebettete Systeme \label{embsystems}

| |`Raspberry-Pi 3b+` |`STM32MP157A-DK1` |
|---|---|---|
|Prozessor |Arm Cortex-A53 |Arm Cortex A7 + Arm Cortex A4 |
|Arbeitsspeicher  |1GB LPDDR2 SDRAM |4-Gbit DDR3L |
|Flash-Speicher |SD-Karte |SD-Karte |
|(+gpio)-Header |ja (40 Pol, (+i2c),(+spi))|ja (40 Pol, (+i2c),(+spi)) |
|Netzwerk|(+lan), (+wlan) |(+lan), (+wlan) |
|Besonderheiten |64-bit Prozessor |Arm Cortex A4 Co-Prozessor, Secure-Boot, Debugger|

Diese bieten vergleichbare technische Spezifikationen und siedeln sich im gleichen Preissegment an.
Je nach Ausführung des `STM32MP157A-DK` ist in diesem bereits ein (+dsi)-Display \ref{stm32mp1} vorhanden und bietet von der Softwareseite her bereits eine Unterstützung für das `Yocto`-Projekt an.
Ein Vorteil des `STM32MP157A-DK` gegenüber dem bekannten `Raspberry-Pi 3b+` ist sein zusätzlicher `Arm Cortex A4`-Co-Prozessor, welcher als zusätzlicher Mikrokontroller verwendet werden kann.
Somit kann die Ansteuerung der (+gpio)-Anschlüsse, sowie Timer und Iterrupt-Aufgaben von diesem übernommen werden und die Ergebnisse und Steuersignale von `Arm Cortex A7` Hauptprozessor und dessen Linux-System bearbeitet werden.

Der `Raspberry-Pi 3b+` hingegen bietet einen großen Software-Support an, welches an der großen Open-Source-Community liegt, welche das Erfolgreiche System über die Jahre aufbauen konnte. Der `Arm Cortex-A53` 64-bit Quad-Core Prozessor bietet dabei viele Leistungsreserven und die (+gpio) Anschlüssen können direkt über das Dateisystem angesteuert werden. Einzig der 1 Gigabyte große Arbeitsspeicher und die Anbindung des Netzwerk-Chips über (+usb) sind der Flaschenhals des Systems.
Somit eignen sich beide Systeme von den Spezifikationen her für diesen Prototypen.

Anschließend wurde eine Test-Software erstellt und mittels des `Buildroot`-Framworks ein passendes Linux-System erstellt. Auf beiden Systemen ist es möglich, dieses auszuführen, jedoch war es nicht möglich, eine mittels `Qt` und der `Quick Controls II`-Erweiterung erstellte (+gui) auf dem `STM32MP157A-DK` auszuführen. Dies liegt am zum Zeitpunkt der Evaluation nicht mit der (+gpu) des Systems lauffähigen Version des `ELGFS`-Frameworks.
Dieses wird verwendet, um Grafik mittels Hardwarebeschleunigung auf dem Display anzeigen zu können. 

Somit wurde nach mehreren Versuchen, dieses Problem zu lösen, das `Raspberry-Pi 3b+`-System als eingebettetes System für den autonomen Schachtisch ausgewählt und die Entwicklung auf diesem fortgesetzt.

## Verifikation NFC Technologie zur Identifizierung der Schachfiguren

Ein weiterer wichtiger Bestandteil sollte die Erkennung der sich auf dem Feld befindlichen Schachfiguren sein.
Hierbei muss zum einen der Figur-Typ (König, Dame, Türme, Läufer, Springer, Bauern) und zum anderen die Figur-Farbe (schwarz, weiss) vom System erkannt werden.

Da hier keine aufwendige Elektronik entwickelt werden, sondern auf Standard-Komponenten zurückgegriffen werden sollte, schied ein (+hf) Antennen-Array unter dem Schachfeld aus, wie es bei einigen kommerziellen Produkten umgesetzt ist.
Eine einfache 8x8 Matrix aus Drucktastern oder Hall-Effekt-Sensoren schied ebenfalls aus, da hier die Eingabe über den Benutzer erfolgt und nur Rückschlüsse auf die veränderte Figur anhand einer manuellen Bewegung der Figur nachvollzogen werden kann.

<br>

Stattdessen eignete sich hier die (+nfc) Technologie, welche auch bei modernen Smartphones eingesetzt wird.
Hierzu werden kleine (+nfc)-Tags bzw. Aufkleber, welche aus einem Chip und einer Antenne bestehen, so programmiert, dass diese eine definierte Aktion beim Lesegerät auslösen.
Dies kann zum Beispiel das Öffnen einer Internetseite auf dem mobilen-Endgerät nach dem Scan eines mit einem NFC Tag ausgestatteten Filmplakats sein.

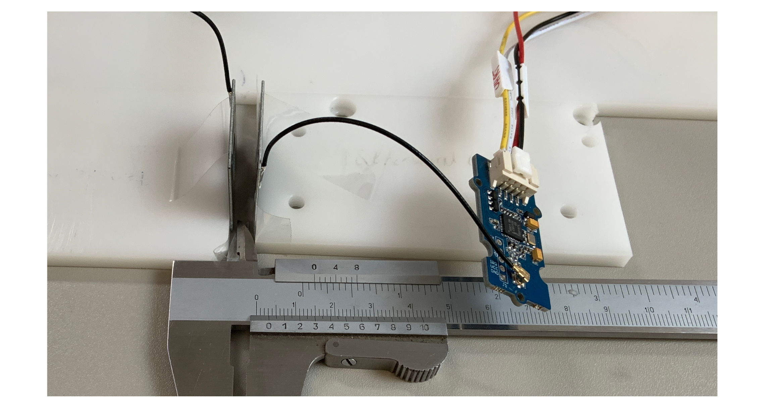
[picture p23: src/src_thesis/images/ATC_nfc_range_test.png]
Grove PN532 NFC Reader mit kabelgebundener Antenne \label{ATC_nfc_range_test}


Ein Vorteil dieser Technologie ist, dass diese auch im Konsumerbereich bereits breit verfügbar ist. Durch das einfache Programmieren dieser (+nfc)-Tags über das Smartphone wird kein zusätzliches Lese-/Schreib-Gerät benötigt.
Hier musste jedoch zuvor getestet werden, welcher maximale Abstand erlaubt ist, um solch einen Tag noch scannen zu können.
Auch ist der Abstand zwischen den einzelnen Tags entscheidend, d.h. wie nah können diese beieinander platziert werden, um trotzdem noch einwandfrei individuell ausgelesen werden zu können.

<br>

Hierzu wurde ein kleiner Testaufbau \ref{ATC_nfc_range_test} entwickelt, um verschiedene Abstände testen zu können.
Als Lesegerät wurde ein `PN532` Modul zum Auslesen der (+nfc) Tags eingesetzt, da dieses Modul einfach angesteuert werden kann und eine abnehmbare Antenne besitzt.
Dieses Modul wurde bereits in anderen Projekten eingesetzt und erwies sich dort als zuverlässig.

<br>

Die im Test verwendeten (+nfc) Tags hatten einen Durchmesser von 22mm und waren somit ein Standard-Produkt.
Im Test stellte sich heraus, dass diese Tags im gewählten Setup einen Abstand von mindestens 5mm zueinander benötigten.
Der Abstand des Lesegeräts bzw. der Antenne zu einem Tag konnte dabei bis zu 14mm betragen.
Somit eignet sich die Kombination aus Tag und Lesegerät für eine Positionserkennung der Schachfiguren, wobei sich das Lesegerät unter der Schachtischplatte befindet.

<br>
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

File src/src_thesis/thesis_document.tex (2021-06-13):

\hypertarget{einleitung}{%
\chapter{Einleitung}\label{einleitung}}

\hypertarget{motivation}{%
\section{Motivation}\label{motivation}}

Eingebettete Systeme (Englisch ``embedded Systems'') sind technische
Zusammensetzungen, die für eine spezifische Funktion entwickelt werden.
Im Gegensatz zu Mehrzwecksystemen (Englisch ``multi-purpose systems''),
wie zum Beispiel einem Personal Computer, der in der Lage ist, diverse
Funktionen auszuführen und nicht zwingend nur an eine Funktion gebunden
ist, dienen eingebettete Systeme einer bestimmten Logik. Daraus
resultieren einfachere und auch ressourcen-schonendere Systeme, die
wesentlich näher an der Technik und der für den Zweck nötigen
Komponenten und Software entwickelt werden. Systeme können günstiger
zusammengesetzt und Fehlerquellen schneller entdeckt und behoben werden.
Nicht für den Prozess notwendige Komponenten werden gar nicht erst
verwendet. Bei einem Mehrzwecksystem wird akzeptiert, dass Komponenten
und Schnittstellen existieren, die nicht benötigt werden. Diese
verursachen Kosten und können mögliche Fehlerquellen sein.

Dennoch ist die Entwicklung eines solchen Systems nicht banal. Es ist
abzuwägen, welche Komponenten derzeit auf dem freien Markt erhältlich
sind, welche Eigenschaften diese mitbringen oder ermöglichen und wie
diese optimal kombiniert werden können. Es bedarf im Vorhinein
intensiver Recherche und einer größeren Perspektive über mögliche
Zusammenhänge. Im Falle eines Mehrzwecksystems ist die Auswahl simpler,
da man den Prozess auch im Nachhinein noch anpassen kann, zusätzliche
Funktionen und Komponenten gegeben sind oder leichter ergänzt werden
können. Das eingebettete System muss in der Regel aufgewertet oder sogar
völlig ersetzt werden, wenn zu einem späteren Zeitpunkt festgestellt
wird, dass Funktionen nicht gegeben oder umsetzbar sind. Fertige Systeme
sind komplexer in der Aufwertung.
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

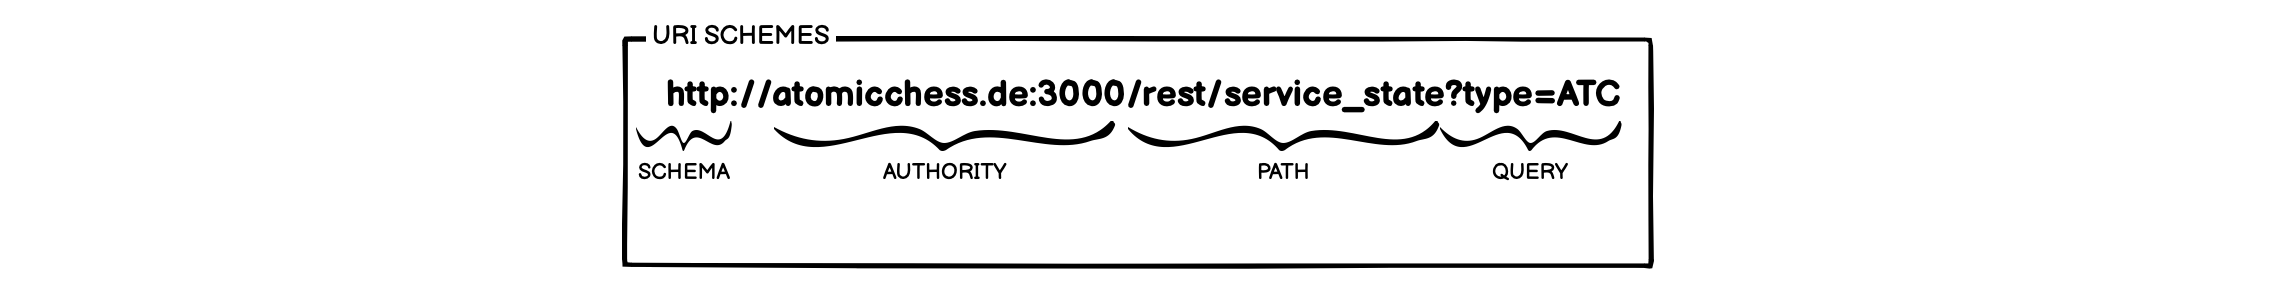
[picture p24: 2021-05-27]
src/src_thesis/images/ATC_URI_SCHEMES.png

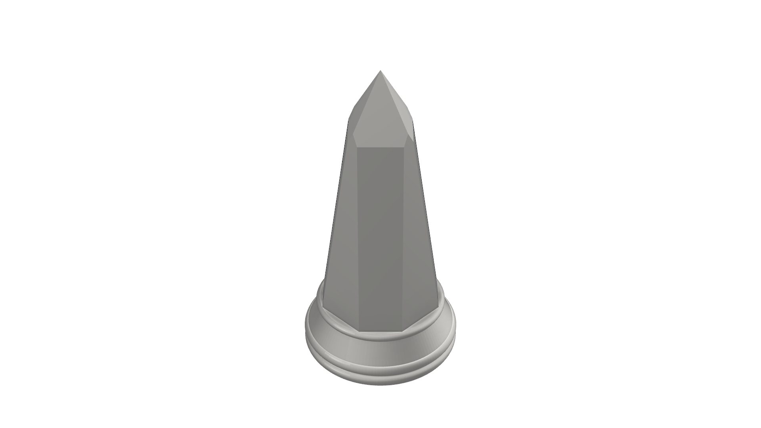
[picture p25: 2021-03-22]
src/src_mechanic/HARDWARE_PROD_V2/CAD/CHESS_FIGURES/IMG/chess_SLA_King.png

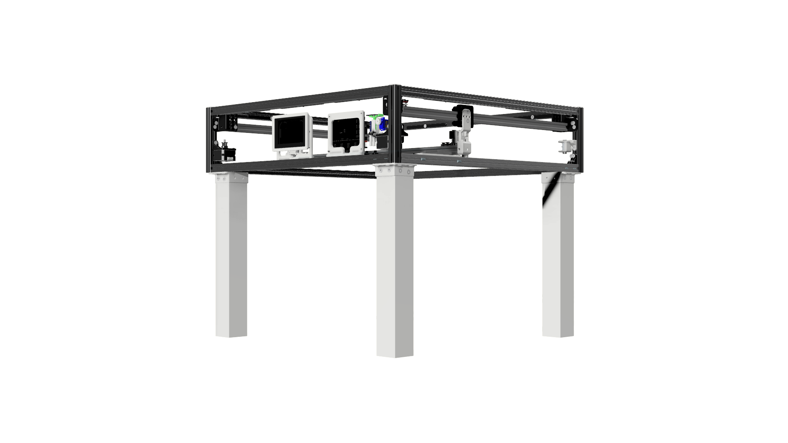
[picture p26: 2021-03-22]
src/src_mechanic/HARDWARE_PROD_V2/IMG/ATC_Table_53_opened.png

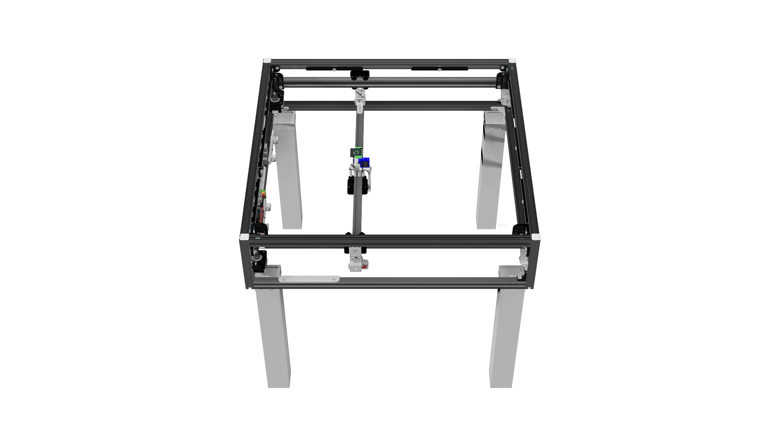
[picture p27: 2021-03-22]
src/src_mechanic/HARDWARE_PROD_V2/IMG/ATC_Table_44_opened.png

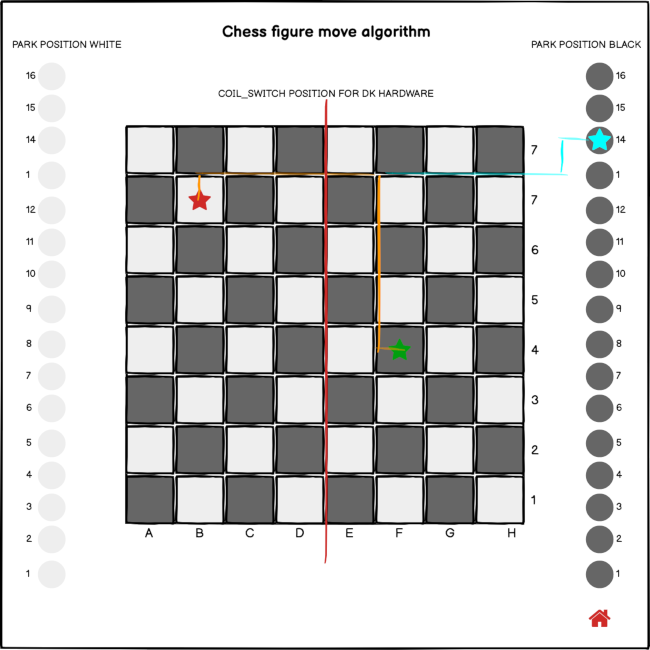
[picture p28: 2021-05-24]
src/src_thesis/images/ATC_FigureMoveAlgorithm_orig.png

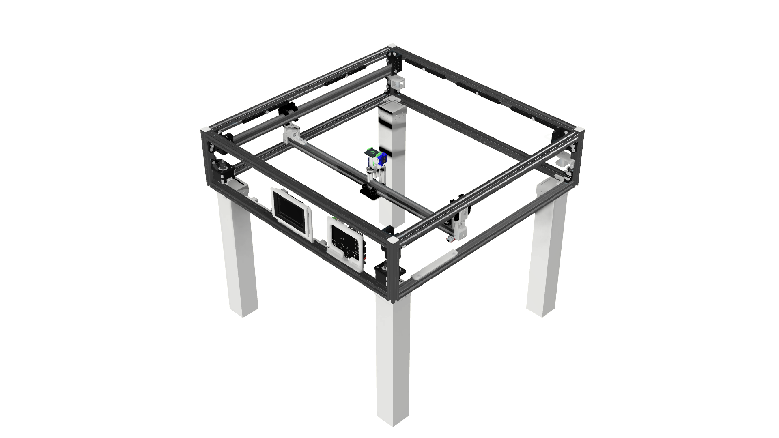
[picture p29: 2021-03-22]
src/src_mechanic/HARDWARE_PROD_V2/IMG/ATC_Table_43_opened.png

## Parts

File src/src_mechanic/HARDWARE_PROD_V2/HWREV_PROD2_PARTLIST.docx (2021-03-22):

Liste aller Bauteile

| Bild | Name | Anzahl | Preis (€] (nur Material) | Preis insgesamt | Infill [%] | Druck-Zeit | Gewicht

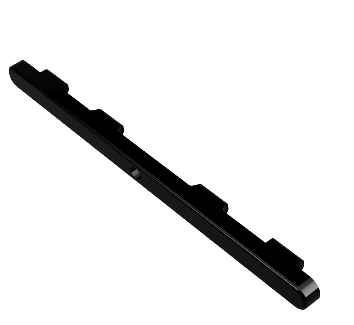
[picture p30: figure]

1 | | ATC_Board_even | 8 | 0,20 | 0,62 | 50 | 0:26 | 9
2 | | ATC_Cable_Guide_inside | 1 | 0,45 | 0,45 | 50 | 0:53 | 21
3 | | ATC_Cable_Guide_outside | 2 | 0,31 | 0,62 | 50 | 0:50 | 16
4 | | ATC_Chess_figure_base | 16 | 0,10 | 1,60 | 50 | 0:10 | 3
5 | | ATC_CornerEdges_large | 4 | 0,10 | 0,40 | 80 | 0:15 | 5
6 | | ATC_CornerEdges_small | 14 | 0,07 | 0,98 | 80 | 0:10 | 3
7 | | ATC_Corner_x_axis_left | 2 | 0,60 | 1,20 | 70 | 1:30 | 28

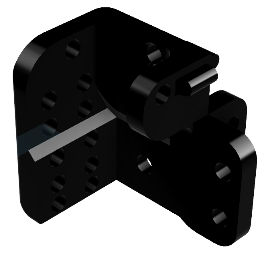
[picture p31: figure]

8 | | ATC_Corner_x_axis_right | 2 | 0,60 | 1,20 | 70 | 1:30 | 28
9 | | ATC_Endswitch_X | 1 | 0,05 | 0,05 | 80 | 0:10 | 2

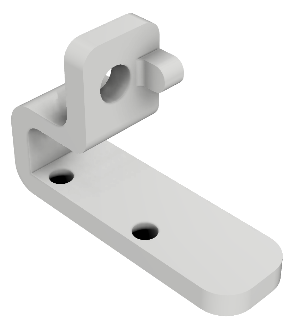
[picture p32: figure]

10 | | ATC_Endswitch_Y | 1 | 0,12 | 0,12 | 50 | 0:17 | 5

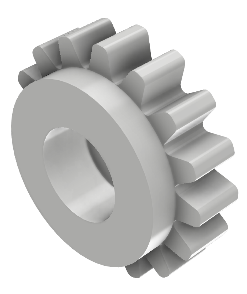
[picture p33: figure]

11 | | ATC_Gear_Mini | 1 | 0,05 | 0,05 | 90 | 0:10 | 2
12 | | ATC_guide_out_figures_all (je 4 Teile) ATC_guide_out_figures_part1 ATC_guide_out_figures_part2 ATC_guide_out_figures_part3 ATC_guide_out_figures_part4 | 2 | 0,60 | 1,20 | 20 | 1:42 | 30

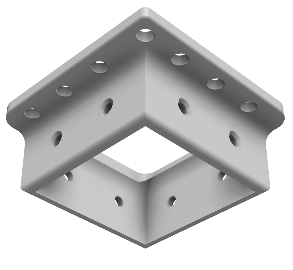
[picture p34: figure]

13 | | ATC_IKEA_leg_item_holder | 4 | 0,75 | 3,00 | 80 | 1:48 | 36
14 | | ATC_Item_Cover | 4 | 0,05 | 0,20 | 80 | 0:10 | 1

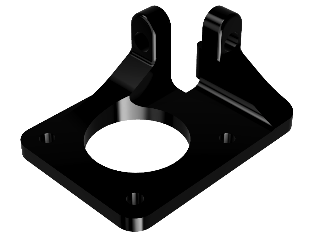
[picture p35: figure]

15 | | ATC_MotorHolder_left | 1 | 0,25 | 0,25 | 70 | 0:40 | 12
16 | | ATC_MotorHolder_right | 1 | 0,25 | 0,25 | 70 | 0:40 | 12

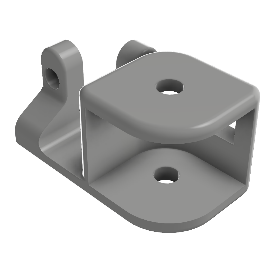
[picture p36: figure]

17 | | ATC_PulleyHolder_left | 1 | 0,40 | 0,40 | 70 | 1:05 | 19
18 | | ATC_PulleyHolder_right | 1 | 0,40 | 0,40 | 70 | 1:05 | 19
19 | | ATC_SKR13_board_mount | 1 | 0,60 | 0,60 | 70 | 1:20 | 29

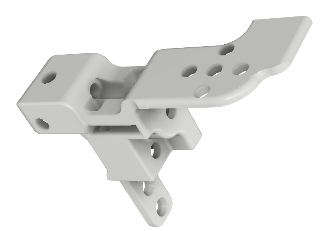
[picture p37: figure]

20 | | ATC_Slider_X_left | 1 | 0,70 | 0,70 | 80 | 2:15 | 35


21 | | ATC_Slider_X_right | 1 | 0,70 | 0,70 | 80 | 2:15 | 34
22 | | ATC_slider_y_all ATC_slider_y_down | 1 | 0,25 | 0,25 | 80 | 0:40 | 12
| | ATC_slider_y_up | 1 | 0,45 | 0,45 | 80 | 1:20 | 22
23 | | ATC_waveshare_display_cover | 1 | 0,50 | 0,50 | 50 | 1:10 | 23
24 | | ATC_waveshare_display_mount | 1 | 0,60 | 0,60 | 50 | 1:20 | 27
25 | | ATC_Zahnstange_NFC | 1 | 0,15 | 0,15 | 80 | 0:50 | 6
26 | | ATC_Zahnstange_simple (nur, wenn Zahnstange_NFC nicht nötig ist) | 0 | 0,10 | 0,00 | 80 | 0:20 | 3
27 | | BT V1.3 R2 SKR1.4 Turbo | 1 | 40,00 | 40,00


28 | | LM2596 DC-DC StepDown Converter | 1 | 3,00 | 3,00


29 | | metal_push_button_17mm | 1 | 2,00 | 2,00
30 | | Rpi3Bplus | 1 | 40,00 | 40,00
31 | | SEEDSTUDIO_NFC_ANTENNA | 1 | 2,00 | 2,00


32 | | SEEDSTUDIO_NFC_READER_PN532 | 1 | 16,00 | 16,00


33 | | SERVO_9G | 1 | 2,00 | 2,00


34 | | Slimline Stepper Motor 0.9deg | 2 | 10,00 | 20,00


35 | | (End-) Switch | 2 | 2,00 | 4,00
36 | | WAVESHARE_4.3_DSI_DISPLAY | 1 | 45,00 | 45,00
37 | | ATC_ChessField_620x620 HOLZ | 1 | 4,00 | 4,00
| | Folie_Chess_Field | 1 | 25,00 | 25,00


38 | | ATC_IKEA_leg_400 | 4 | 1,75 | 7,00


39 | | ATC_Plexiglas_620x120_Display | 1 | 5,00 | 5,00
40 | | ATC_Plexiglas_620x120_full | 3 | 5,00 | 15,00


41 | | ball-bearing 689 2RS 9 x 17 x 5 Rillenkugellager | 8 | 1,00 | 8,00


42 | | DIN 508, T-Slot Nut M5 | 100 | 0,30 | 3,00
43 | | M3x10 | 100 | 0,05 | 5,00


44 | | M3_NUT | 100 | 0,05 | 5,00


45 | | M5x10_HEX | 100 | 0,05 | 5,00
46 | | M5x14_HEX | 100 | 0,06 | 6,00
47 | | M5x25_HEX | 100 | 0,07 | 7,00
48 | | M5x30_HEX | 100 | 0,08 | 8,00


49 | | M5_NUT | 100 | 0,05 | 5,00


50 | | pulley_motor_2GT_20T | 2 | 1,00 | 2,00


51 | | pulley_small_2GT_20T | 4 | 0,50 | 2,00
52 | | VSLOT_20x20_620 mm x-Achsen | 2 | 6,00 | 12,00
53 | | VSLOT 20x20 mm ≤59,5cm Y-Achse | 1 | 5,80 | 5,80
| | ITEM 20x20 mm 640 mm Außen-Rahmen | 8 | 3,00 | 24,00
54 | | ITEM 20x20 mm 160 mm Säulen | 4 | 0,65 | 2,60
55 | | VSLOT_20x20_ROLLER_50mm | 3 | 15,00 | 45,00
56 | | chess_FDM_bishop je eine weiß / schwarz | 0 | 0,60 | 0
57 | | chess_FDM_king je eine weiß / schwarz | 0 | 0,60 | 0
58 | | chess_FDM_knight je eine weiß / schwarz | 0 | 0,60 | 0
59 | | chess_FDM_pawn je eine weiß / schwarz | 0 | 0,60 | 0
60 | | chess_FDM_queen je eine weiß / schwarz | 0 | 0,60 | 0
61 | | chess_FDM_rook je eine weiß / schwarz | 0 | 0,60 | 0
62 | | chess_SLA_Bishop je eine weiß / schwarz | 2 | 1,50 | 3,00
63 | | chess_SLA_King je eine weiß / schwarz | 2 | 1,50 | 3,00
64 | | chess_SLA_Knight je eine weiß / schwarz | 2 | 1,50 | 3,00
65 | | chess_SLA_Pawn je eine weiß / schwarz | 2 | 1,50 | 3,00
66 | | chess_SLA_Queen je eine weiß / schwarz | 2 | 1,50 | 3,00
67 | | chess_SLA_Rook je eine weiß / schwarz | 2 | 1,50 | 3,00
| | SUMME | 956 | 256,91 | 407,34 | 50-90% | 25:01:00 | 442
A | B | C | D Anzahl | E Einzel-preis | F Summe Preis | G Infill | H Zeit | I Gewicht

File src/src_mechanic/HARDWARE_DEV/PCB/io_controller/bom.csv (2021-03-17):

ID | Name | Designator | Footprint | Quantity | Manufacturer Part | Manufacturer | Supplier | Supplier Part
1 | TMC5160-BOB | DRV1,DRV2 | TMC5160-BOB | 2 |  | TRINAMIC MOTION CONTROL GmbH
2 | Fuse transparent seat | F1,F2 | FUSE-TH_L22.6-W9.0 | 2 | Fuse transparent seat | ReliaPro | LCSC | C58066
3 | Header-Male-2.54_1x3 | H5,H6,H8,H9,H10,H12,H13 | HDR-TH_3P-P2.54-V | 7 | Header2.54mm 1*3P | BOOMELE | LCSC | C49257
4 | Header-Male-2.54_1x4 | H1,H2,H3,H4,H7,H11 | HDR-TH_4P-P2.54-V | 6 | 210S-1*4P L=11.6MMGold-plated black | Ckmtw | LCSC | C124378
5 | 1125S-4P | J1 | HW4-2.0 | 1 | 1125S-4P
6 | RPI3B+_Header | J2 | 2X20_2.54_HEADER | 1 | 61304021121 |  | Digi-Key | 732-5310-ND
7 | LM1117T-3.3 | LD31 | T03B | 1 |  | National Semiconductor
8 | LED5MM | LED1,LED2,LED3,LED4 | LED5MM | 4
9 | 2.54mm 1*2P | P1,P2,P3,P4,P5,P6,P7 | HDR-TH_2P-P2.54-V-M | 7 | 2.54mm 1*2P | ReliaPro | LCSC | C36717
10 | Potentiometer | POT1 | MY_POT | 1 | potentiometer
11 | Resistor 1/8W THT | R1,R2,R3,R4,R5,R6,R7,R8,R9,R10,R11,R12,R13 | RESISTOR 1/8W THT | 13 | Generic | Generic | Mouser | Generic
12 | ArduinoNano | U1 | ARDUINO NANO VINCENT | 1 | ArduinoNano
13 | Mini 360 converter 1.8A | U2 | MINI 360 STEP DOWN CONVERTER 1.8A | 1 | Mini 360 step down converter 1.8A
14 | LM2596 | U3 | STEP_DOWN_LM2596S | 1
15 | LevelShifter | U4 | 12PIN | 1
16 | DRV8833 | U5 | DRV8833 MOTOR DRIVER | 1

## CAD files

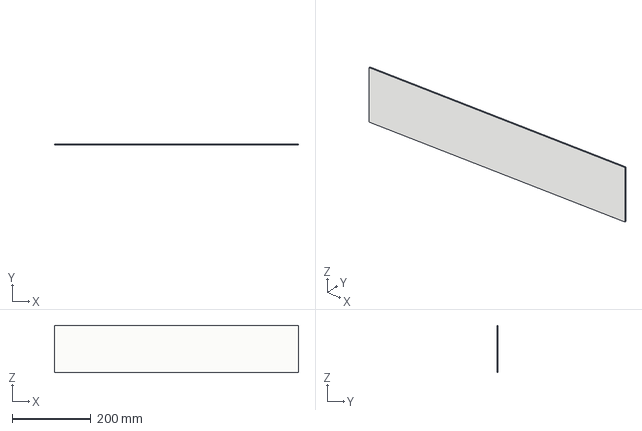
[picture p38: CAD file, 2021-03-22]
src/src_mechanic/HARDWARE_PROD_V2/CAD/MISC_PARTS/ATC_Plexiglas_620x120_full.step
620.0 x 3.00 x 120.0 mm

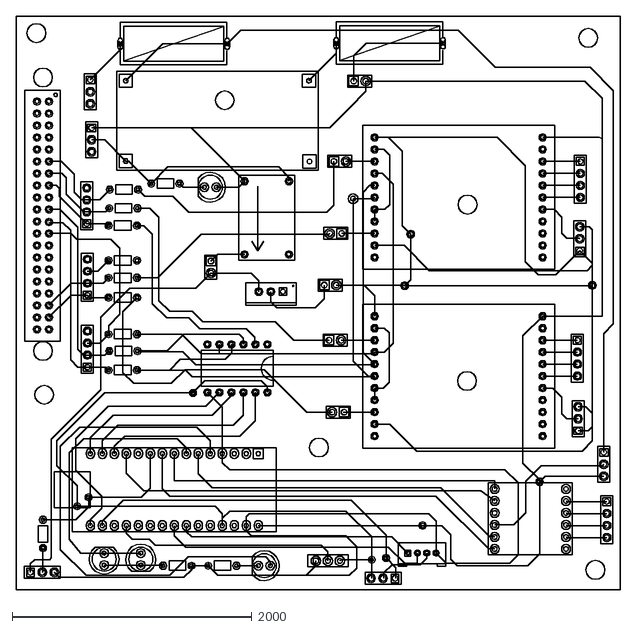
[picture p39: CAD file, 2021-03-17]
src/src_mechanic/HARDWARE_DEV/PCB/io_controller/board.dxf
5035.0 x 4780.0

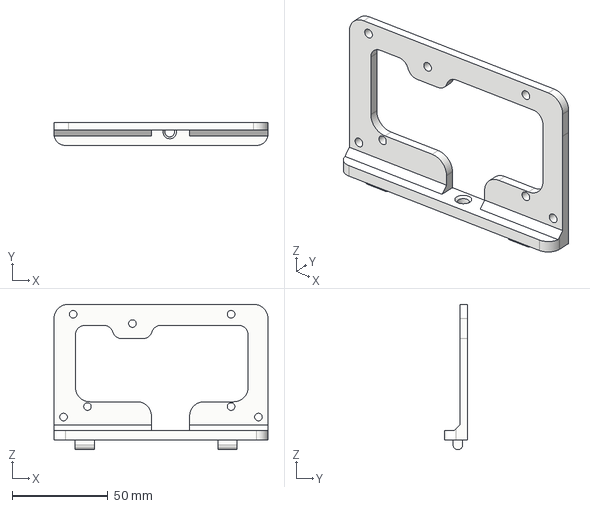
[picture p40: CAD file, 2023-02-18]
src/src_mechanic/HARDWARE_PROD_V2/CAD/3D_PRINTED_PARTS/STEP/ATC_ARDUINO_MEGA_board_mount.step
112.0 x 12.0 x 76.1 mm

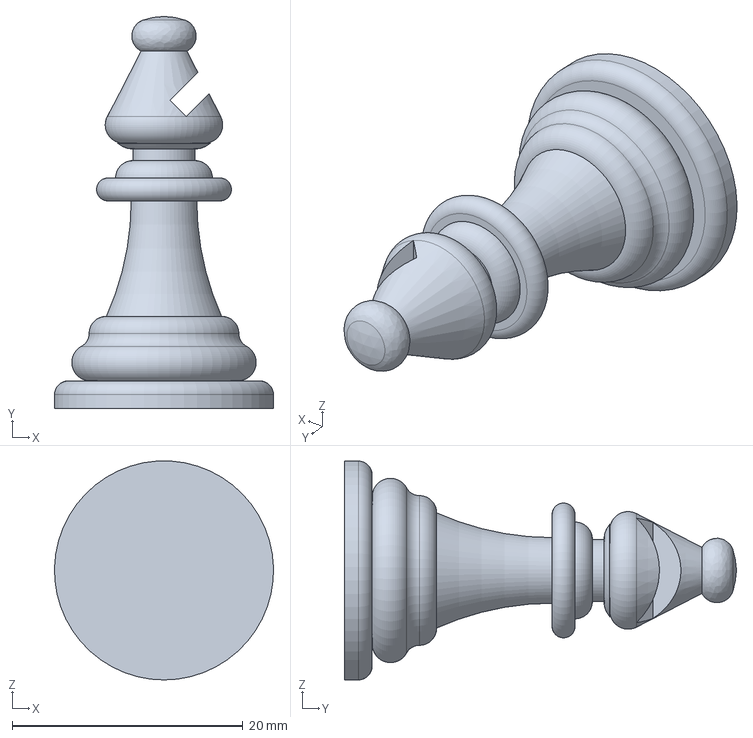
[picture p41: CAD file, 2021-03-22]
src/src_mechanic/HARDWARE_PROD_V2/CAD/CHESS_FIGURES/STEP/chess_FDM_bishop.step
19.0 x 34.0 x 19.0 mm

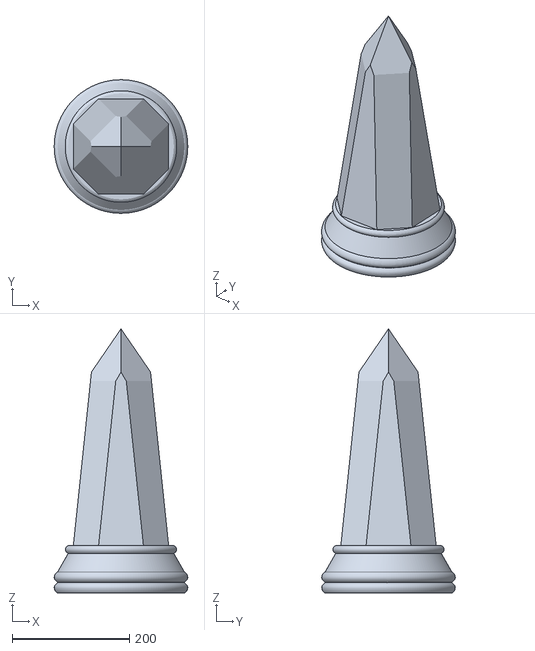
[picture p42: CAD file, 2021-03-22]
src/src_mechanic/HARDWARE_PROD_V2/CAD/CHESS_FIGURES/STL/chess_SLA_King.stl
227.6 x 227.6 x 450.0

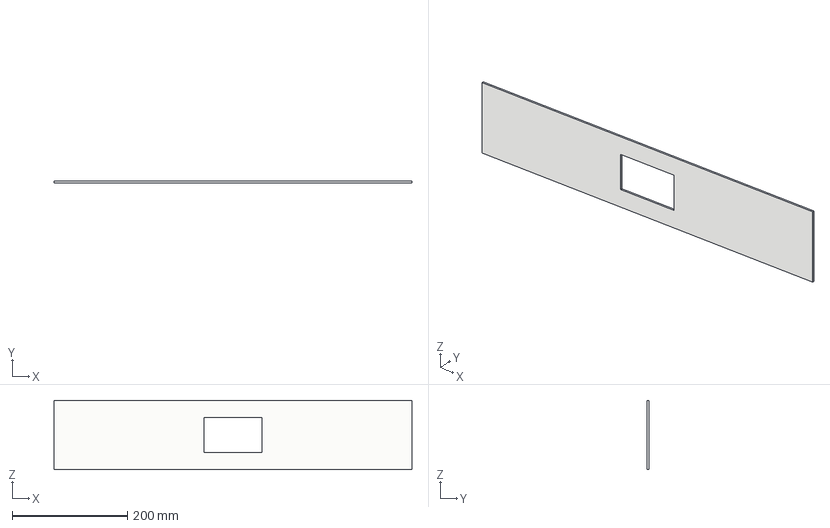
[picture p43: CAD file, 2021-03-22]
src/src_mechanic/HARDWARE_PROD_V2/CAD/MISC_PARTS/ATC_Plexiglas_620x120_Display.step
620.0 x 3.00 x 120.0 mm

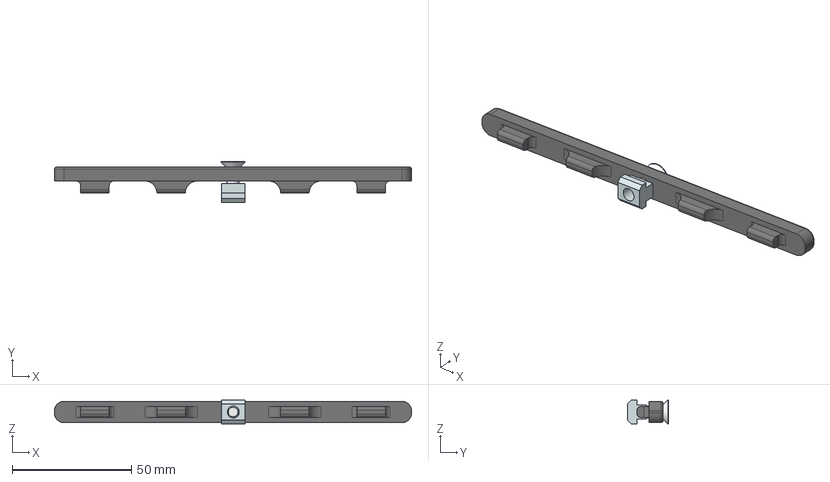
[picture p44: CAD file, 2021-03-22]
src/src_mechanic/HARDWARE_PROD_V2/CAD/3D_PRINTED_PARTS/STEP/ATC_Board_even.step
150.0 x 17.2 x 10.0 mm
ATC_DIN 508, T-Slot Nut M5
ATC_M5x10_HEX

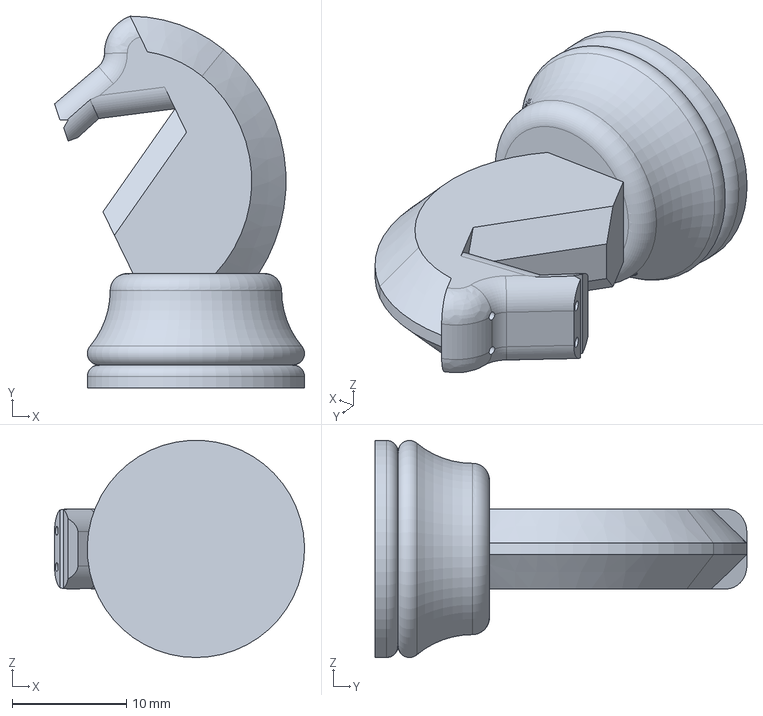
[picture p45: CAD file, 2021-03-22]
src/src_mechanic/HARDWARE_PROD_V2/CAD/CHESS_FIGURES/STEP/chess_FDM_knight.step
21.9 x 32.5 x 19.0 mm

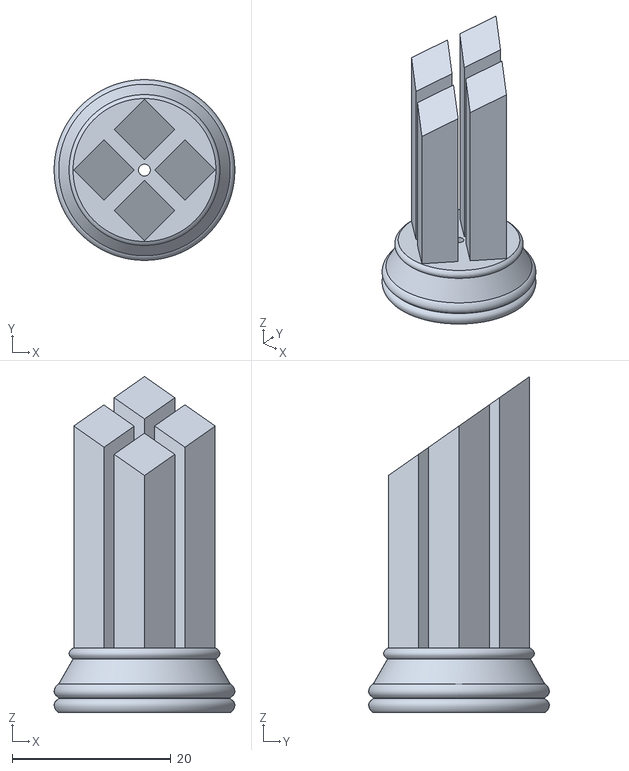
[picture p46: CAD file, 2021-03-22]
src/src_mechanic/HARDWARE_PROD_V2/CAD/CHESS_FIGURES/STL/chess_SLA_Rook.stl
22.8 x 22.8 x 42.3

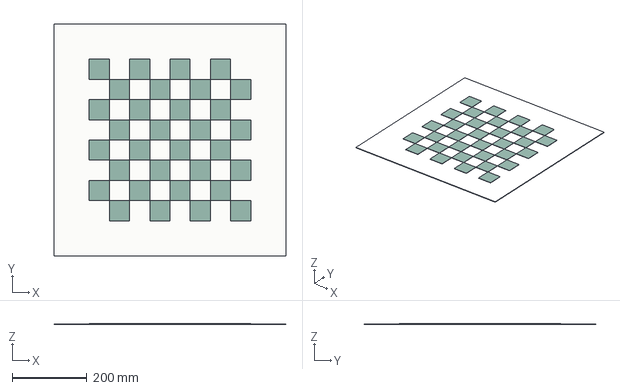
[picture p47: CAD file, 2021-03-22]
src/src_mechanic/HARDWARE_PROD_V2/CAD/MISC_PARTS/ATC_ChessField_620x620.step
620.0 x 620.0 x 3.00 mm

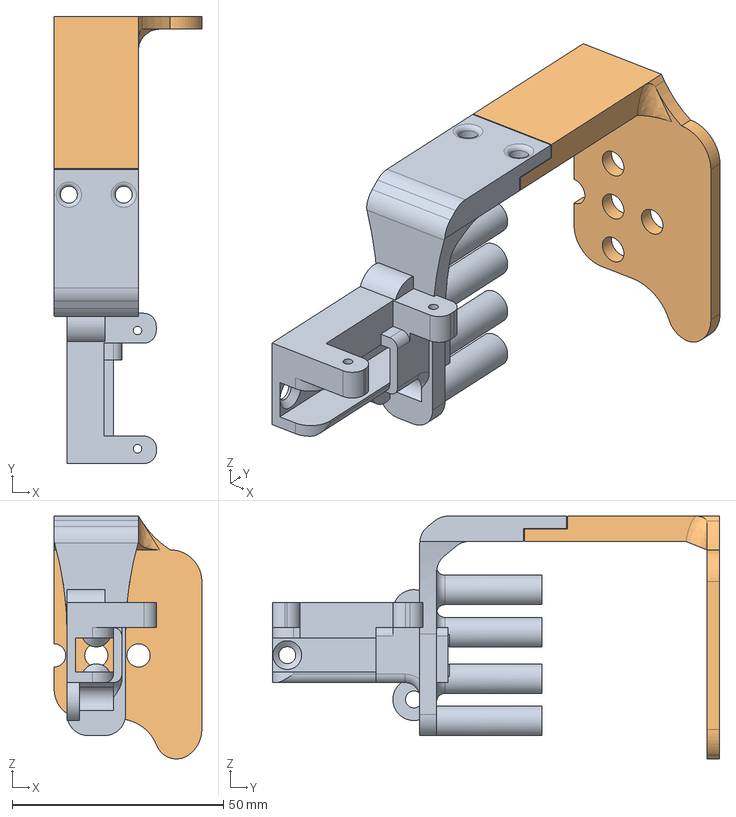
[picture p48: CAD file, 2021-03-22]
src/src_mechanic/HARDWARE_PROD_V2/CAD/3D_PRINTED_PARTS/STEP/ATC_slider_y_all.step
35.0 x 105.9 x 57.5 mm

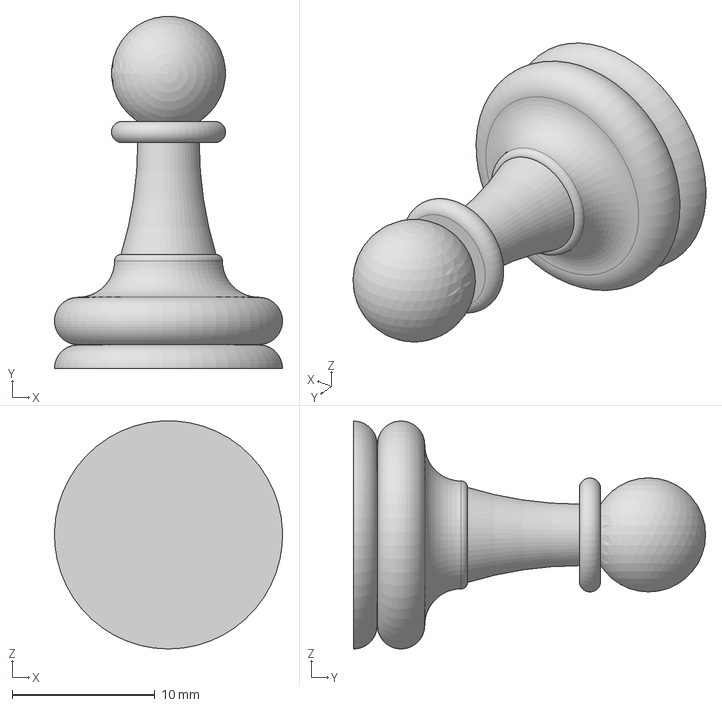
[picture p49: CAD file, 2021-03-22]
src/src_mechanic/HARDWARE_PROD_V2/CAD/CHESS_FIGURES/STEP/chess_FDM_pawn.step
16.0 x 24.7 x 16.0 mm

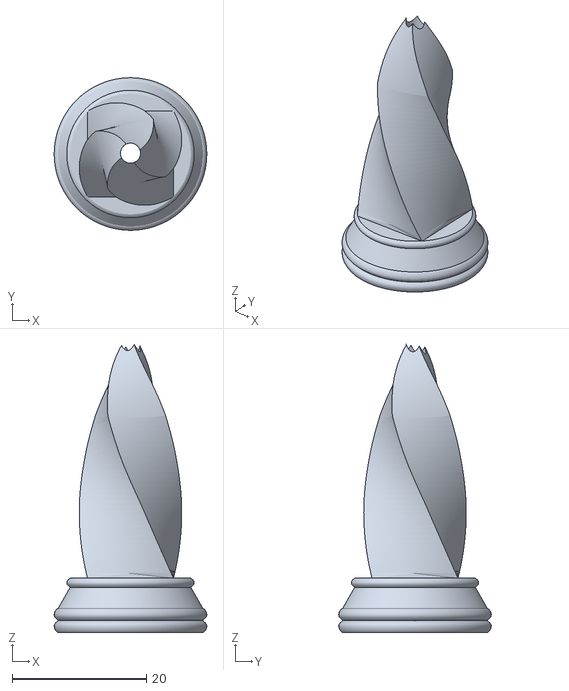
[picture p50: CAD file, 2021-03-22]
src/src_mechanic/HARDWARE_PROD_V2/CAD/CHESS_FIGURES/STL/chess_SLA_Queen.stl
22.8 x 22.8 x 43.0

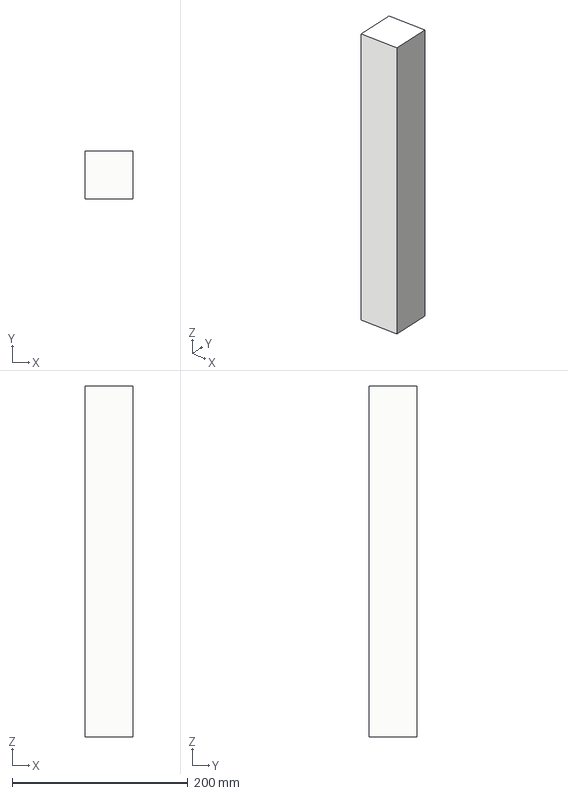
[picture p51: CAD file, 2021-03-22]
src/src_mechanic/HARDWARE_PROD_V2/CAD/MISC_PARTS/ATC_IKEA_leg_400.step
55.0 x 55.0 x 400.0 mm

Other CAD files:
src/src_mechanic/HARDWARE_PROD_V2/CAD/3D_PRINTED_PARTS/STEP/ATC_CornerEdges_small.step
src/src_mechanic/HARDWARE_PROD_V2/CAD/CHESS_FIGURES/STEP/chess_FDM_king.step
src/src_mechanic/HARDWARE_PROD_V2/CAD/CHESS_FIGURES/STL/chess_SLA_Bishop.stl
src/src_mechanic/HARDWARE_PROD_V2/CAD/3D_PRINTED_PARTS/STEP/ATC_Zahnstange_NFC.step
src/src_mechanic/HARDWARE_PROD_V2/CAD/3D_PRINTED_PARTS/STEP/ATC_Cable_Guide_inside.step
src/src_mechanic/HARDWARE_PROD_V2/CAD/3D_PRINTED_PARTS/STEP/ATC_Cable_Guide_outside.step
src/src_mechanic/HARDWARE_PROD_V2/CAD/3D_PRINTED_PARTS/STEP/ATC_Chess_figure_base.step
src/src_mechanic/HARDWARE_PROD_V2/CAD/3D_PRINTED_PARTS/STEP/ATC_CornerEdges_large.step
src/src_mechanic/HARDWARE_PROD_V2/CAD/3D_PRINTED_PARTS/STEP/ATC_Endswitch_X.step
src/src_mechanic/HARDWARE_PROD_V2/CAD/3D_PRINTED_PARTS/STEP/ATC_Endswitch_Y.step
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

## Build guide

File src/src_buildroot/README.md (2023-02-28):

# BUILDROOT

This branch contains the buildroot framework to build the AtomicChessOS.

The buildroot configuration is stored under `./buildroot/config_backup`

# GETTING STARTED

Only a few commands are needed to build the AtomicChessOS Image with all needed software packages and ready to use.

```bash
$ sudo apt  update && apt  upgrade -y
$ sudo apt install git-all
$ sudo apt install software-properties-common libncurses-dev python3 python3-pip python3-dev python3-setuptools python3-wheel ninja-build libcap-dev libmount-dev

# !!! INSTALL DOCKER !!! (or execute ./buildroot/build.sh twice if you dont want to use docker)
# SEE https://docs.docker.com/desktop/install/linux-install/

# COPY CUSTOM PACKAGES
$ bash ./copy_local_packages.sh

# CREATE DOCKER IMAGE
$ bash ./buildroot/build_docker_image.sh

# GENERATE SWUPDATE FIRMWARE UPDATE SIGNING KEYS
$ bash ./buildroot/SWUPDATE/generate_keys.sh

### RUN THE FOLLOWING COMMANDS IF YOU WANT TO BUILD A SDCARD IMAGE AND FIRMWARE UPDATE FILE
### BUT RUN IT AT LEAST ONCE !
### CAN TAKE UP TO FOUR HOURS, ON FIRST TIME RUN
### REQUIRES ABOUT 20GB OF FREE DISK SPACE TO DOWNLOAD PACKAGE SOURCES

# BUILD THE IMAGE USING DOCKER
# also creates singned swupdate package
# adds double copy update strategy
$ sudo bash ./build_toolchain_image.sh

# FLASH IMAGE
## replace target disk
$ dd if=./buildroot/output/images/sdcard.img of=/dev/rdiskXxX bs=1m
```

# NOTES

## OVERVIEW BUILDROOT

### GOAL OF THIS CHAPTER
The setup of buildroot framework is nessessarcy in order to build the other software components.
* cross compile toolchain is nessessarcy

### WHAT IS BUILDROOT

Buildroot is s software framework that automates the process of building a complete Linux Images for many embedded systems.
It also generate a cross compilation toolchain for the host system.
Buildroot not only generates a host site toolchain, it also generates the target file system with compiled kernel and bootloader.

"Buildroot is useful mainly for people working with embedded systems. Embedded systems often use processors that are not the regular x86 processors everyone is used to having in his PC. They can be PowerPC processors, MIPS processors, ARM processors, etc.
Buildroot supports numerous processors and their variants; it also comes with default configurations for several boards available off-the-shelf."

[SOURCE](https://buildroot.org/downloads/manual/manual.html#_about_buildroot)

### HOW BUILDROOT WORKS

* image
* configration files

### SYSTEM REQUIREMENTS

In order to get the buildrootpackage running, the host linux system need some packages.
All follwing steps are tested on a `Ubuntu 20.04 x64`
These packages can be installed with the `$ sudo apt install <PACKAGE>` command, the `$ sudo apt  update` command might be necessary, to get the latest versions.

* `$ sudo apt  update && apt  upgrade -y`
* `$ sudo apt install git-all`
* `$ sudo apt install software-properties-common libncurses-dev` ython3 python3-pip python3-dev python3-setuptools python3-wheel ninja-build libcap-dev libmount-dev

* `$ sudo apt install sed make binutils build-essential socat gcc g++ gzip bzip2 perl tar cpio unzip rsync bc wget git python cpio sed cmake genext2fs libssl-dev  -y`
* `$ sudo apt install gtk2.0 gtk2.0-dev csv python-glade2 libncurses5 libncurses5-dev -y`

For documentation using `Doxygen` the `doxygen` packages is needed. Also the `graphviz` is nessessary, to allow `doxygen` to generate visual call-graphs.

* `$ sudo apt install doxygen doxygen-gui graphviz -y`

The installation took place on a fresh installed Ubuntu 20.04, where most of the packages are already installed.

[SOURCE](https://buildroot.org/downloads/manual/manual.html#requirement)

#### INSTALL BUILDROOT

For this project a complete configured buildroot installation can be found in the git repository:
`/src/src_buildroot/buildroot`. All commands listed in this chapter are relative to this path.

Its also possible to create a fresh installation of buildroot. The base version of buildroot used in this project, was the release number `2020.02` which can be found on the buildroot download page `https://buildroot.org/download.html`.

After downloading the `tar.gz` file from the downloadpage. The archive must be unpacked using the `tar` command:

`$ tar -xf Downloads/buildroot-2020.02.tar.gz`

The setup of buildroot is finished after extraction process is complete.

## BASIC CONFIGURATION

To create a basic configuration buildroot provied a set of template boards/architectures to setup a minimal running configuration.
All avariable configuration can be found in the boards folder `./board`. Our Target Sytem is the RaspberryPi 3b+, there is a template for this already in the board folder and can be loaded with the `make <BOARD_NAME>_defconfig`. After running `$ make raspberrypi3_defconfig`, the buildroot config file `./.config` contains all needed parameters and packages.

Buildroot offer a terminal based grahpical menu, to select the right options and packages to install.
To access the menu, simply call `$ make menuconfig` inside of the buildroot root folder.
The following screen appears in the current terminal window:

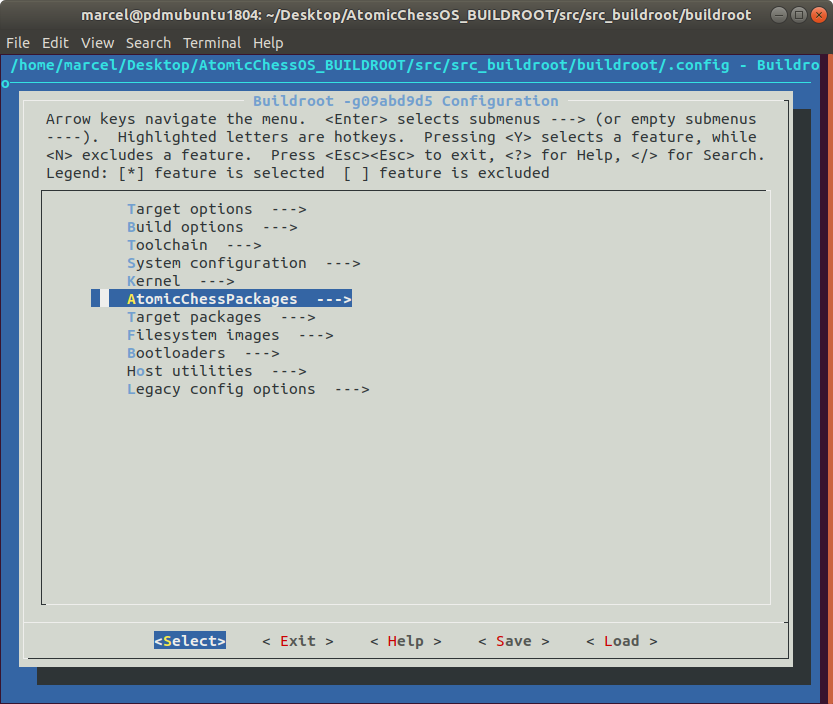
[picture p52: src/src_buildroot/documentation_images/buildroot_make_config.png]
make menuconfig


The menu is split into several categories and the most important basic configuration points are explained below.

### Target options

* `Target options -> Target Architecture`, the RPI uses an ARM CPU, so the setting is set to `ARM (little endian)`
* `Target options -> Target Architecture Variant`, defines the specific CPU Model. In the RPI3b+ case its an `Cortex A53`

### Kernel

#### KERNEL CONFIGURATION

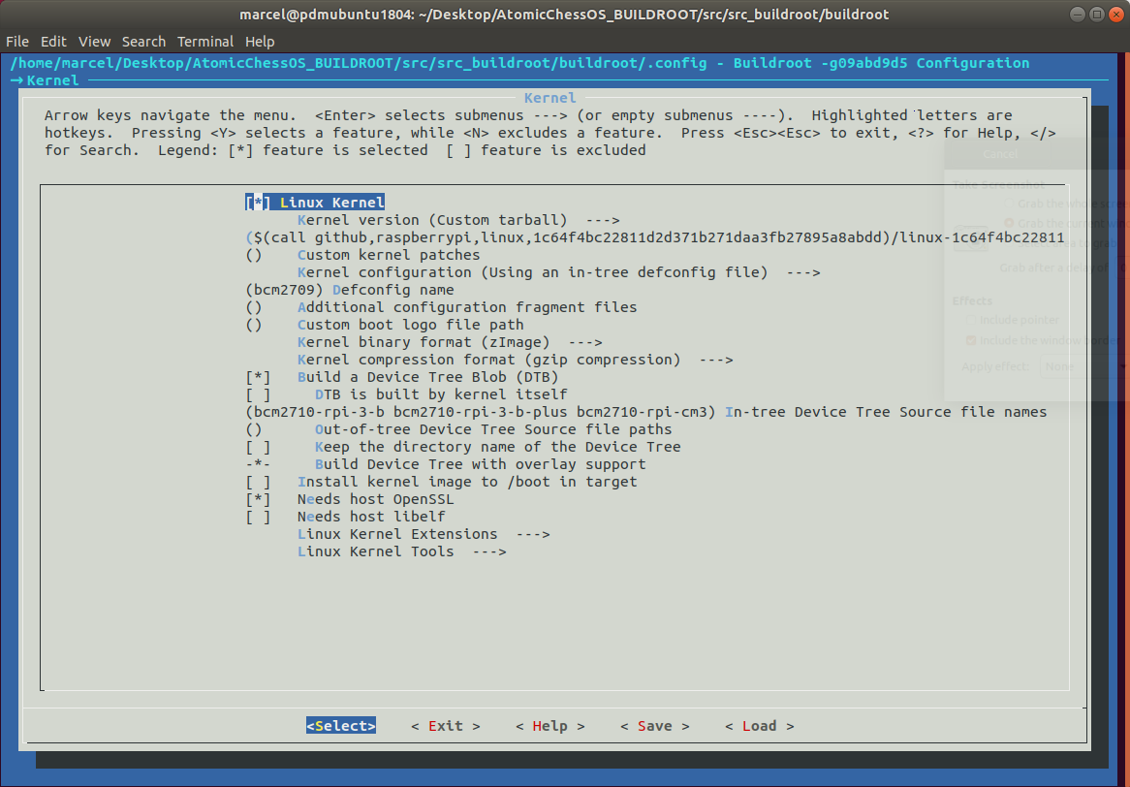
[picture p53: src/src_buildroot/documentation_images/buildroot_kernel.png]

?? WHAT IS A DEVICE TREE ??

* `Kernel -> Device Tree Settings`, this point defines which device tree to build. In this case the predefined device tree `bcm-2710-rpi3b` is used. The DTB `DeviceTreeBinary` Files are downloaded from the RaspberryPi-Firmware Repository automaticly form buildroot.

Its also possible to add additional Device Tree Overlays in additon to the predefined overlay. This is the case if we want to add additional hardware to the target system. In our case, we add a an DTD Overlay to the system, to access the Touchscreen.
The tocuhscreen controller used, is the FT 5406. This controller is also used in the original 7" Raspberry Pi FTF Display, so there is a DTD Overlayfile already existing for loading.
The DTB File can be found in the RaspverryPi-Firmware Repository `rpi-firmware/overlays/rpi-ft5406-overlay.dtb`. We have to make shure that this file exists in the boot partition `<SD_CARD>/boot/overlays/` of the final image.
All DTB files will be loaded at startup if nessessarry. Its also possible to load additional DTB files with the configuration file `/boot/config.txt` of the Raspberry-Pi firmware.

* `Kernel -> Kernel Version`, in this case the precompiled kernel was used which are downloaded form the RaspberryPi-GitHub-Repository.

These are basic nedded configuration items to setup a minimum booting system.
Also buildroot generates a cross-compiler for the host system. So its possible to build software for the target-system.

The next step is the system configuration and the target packages configuration.

### TOOLCHAIN

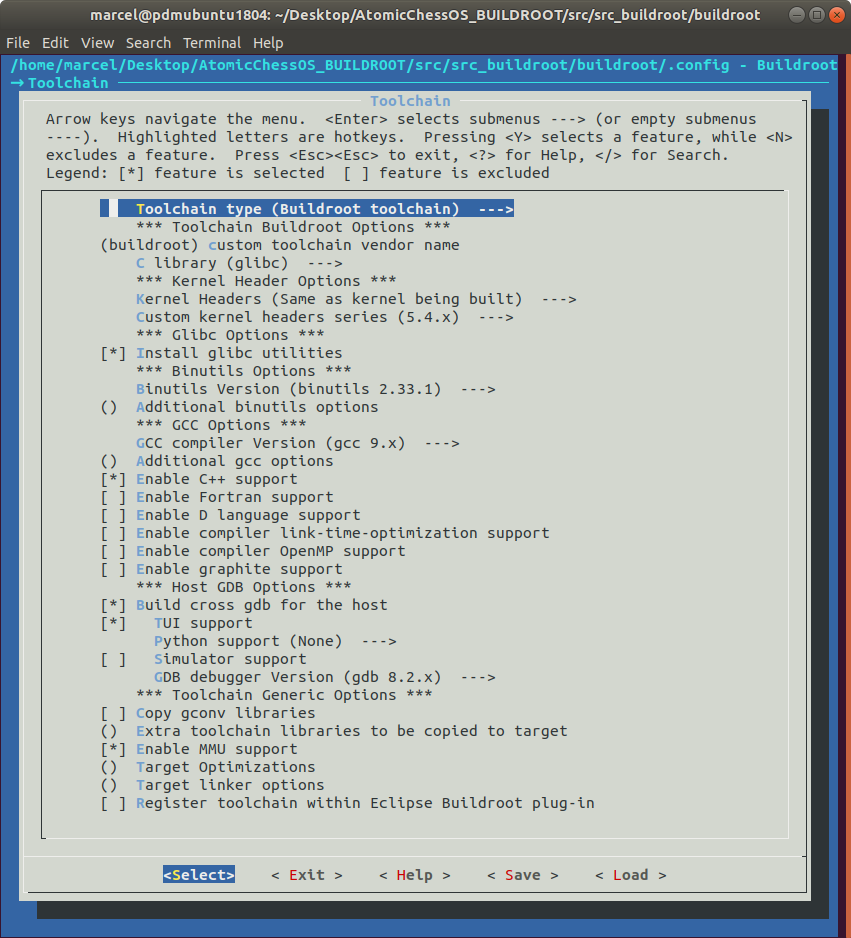
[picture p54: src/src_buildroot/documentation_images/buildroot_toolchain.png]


The buildroot framework does not only build a image for the target device, it also build all nessessary tools for build software for the target. This software collection is called toolchain and in runnung on the host system. On the target plattform is no compiler or build system installed, so its nit possible to compile software directly on the target, with an buildroot image.

#### SITENOTE_TOOLCHAIN

With the standard raspian os for the raspberry pi, its possible to install an compiler like gcc and a buildsystem like make, directly on the raspberry pi.

#### END SITENOTE

In the `Toolchain` Menu, its possible to setup, all parameters for the host toolchain that buildroot builds, together with the target image.
For example its possible to install a GCC or a Fortran compiler into the toolchain.
For development, we need a C++ compiler and a debugger.
The GDB Debugger has to be installed on the target and on the host. Buildroot selects the right version for host and target.

* `Toolchain -> Enable C++ support` -> enables the gcc and g++ compiler with the make build system
* `Toolchain -> Build Cross GDB` -> build the GDB Debugger for host and target

All other settings are the default settings. Its also possible to register the toolchain to an IDE linke Eclipse for easier setup on the host side.

### SYSTEM CONFIGURATION

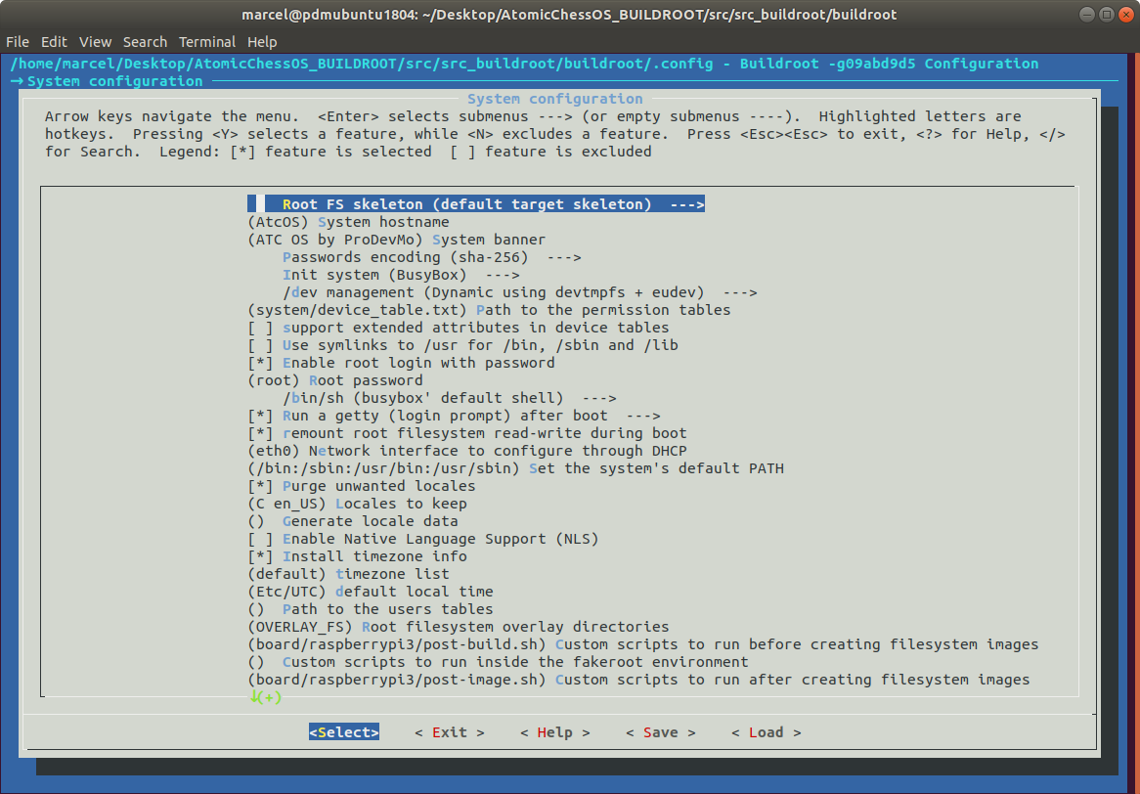
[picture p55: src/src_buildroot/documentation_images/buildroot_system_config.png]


The system configuration allows to setup a root user, password or which keyboard layout should be used. Its like the `$ sudo raspi-config` command in a regular Raspbian installation.

The `System-Configuration` Settings comes also with predefined values. There are only some which needed to be modified.

* `System-Configuration -> Networkinterface DHCP`, this setting defined the Ethernet Interface to enable at startup and using a DHCP Server to obtain a IPv4 Adress. The value on a stock RPI3b+ can be ETH0 (LAN) or wlan0 (WIFI). The ATC_Table is using ethernet as its main network interface so `eth0` is the right choice.

* `System-Configuration -> Root filesystem overlay dir`, this filepath represents the Overlay Directory and is a custom Folder. All files in this directory will be copies into the final image rootfs and replaces existing files. In our case, this will be used for the wifi configuration and other ssh configuration files.

For debugging purposes, the access to the root aacount though a password is acceptable. In the production build of the image, the root access is disbaled.

#### /DEV MANAGEMENT

The setting for the /dev managemtns is very important! The ATC_OS need user interaction thought an input device, like a mouse, keyboard or a touchscreen. By default the udev is disbaled on the system, so its not possible to simply adding a touchscreen input to the system.

* `System Configuration -> /dev management (devtmpfs + eudev)`, enables udev subsystem.

UDEV basicly handles the events coming from an input source (Keyboard,.., plugged Harddrive) and performing tasks based in this inputs.
On task is to load a driver if can keyboard is attached though an usb port. In our case its used to access the touchscreen, after connecting the display via the DSI Interface to the Raspberry Pi, udev loads the FT5406 Touchscreen IC driver and make it accessable as `/dev/input/mouse1` (a usb mice is already plugged in).

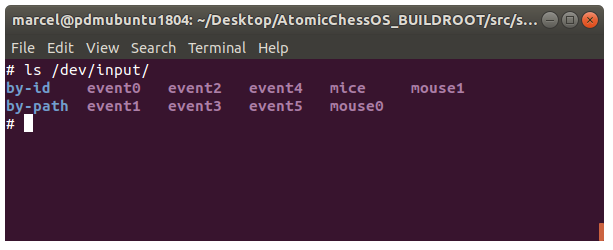
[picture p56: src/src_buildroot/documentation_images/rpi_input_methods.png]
/DEV_FOLDER


### TARGET PACKAGES CONFIGURATION

The target package configuration allows to install software and libraries on the target. For example we want to install an ftp server onto the target. In the target packages we can select the ftpserver packe and all other needed dependencies will be installed too.
Its a very simple process, just select the software and all other needed packages will selected too.

#### QT5

The most important library is the QT5 framework.
The userinterface of the ATC_OS  called ATC_UI is based on QT5 with the QuickControls II extention, so a QT Version >=5.7 is needed to enable this feature.
Buildroot supports the QT5.6 LTS version and the latest QT5.12 version by default. So here we have simply to enable the QT5 packge with all extetion packages.

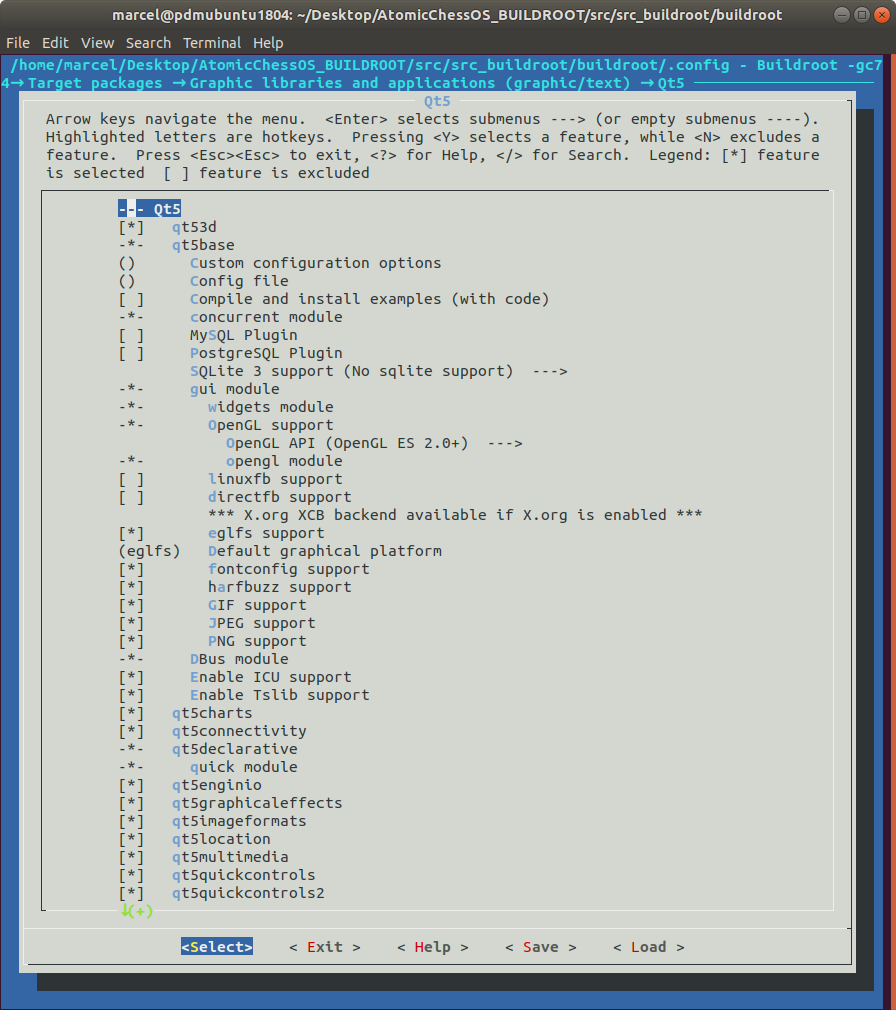
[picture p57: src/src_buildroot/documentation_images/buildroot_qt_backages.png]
QT_PACKAGES_SELECTED


After enabling the QT5 packge, buildroot automaticly enabled EGLFS as grahpics backend. The backend is needed to enable application to render and show graphics on the screen. EGLFS is able to make use of the GPU for graphics acceleration and is needed by the QT5 QuickControl II Extention to render animations.

QT5 alone is able to use other graphics backend too, for example the directfb. the directfb is the simplest graphics backend provided by the linux system, and it can be used for very simple applications.

* `Target Packages -> Graphic -> QT5`, enables QT5, with the QT5_BASIC package. Use the `Return-Key` to access all QT5 packages.
* `Target Packages -> Graphic -> QT5 -> Default Graphic Plattform (ELGFS)`, set the default graphic backend to ELGFS for Hardware Graphics Acceleration.
  
The `Default Graphic Plattform (ELGFS)` entry is important to check, if its not set, the ATC_UI application will not start. The setting sets a environment variable called `QT_QPA_PLATFORM`, which tells the QT5 application to use the ELGFS backend.

#### SSH

In the case of the ATC_OS we need a ssh server to connect to the target via ethernet. This allows the remote debugging and development of the software. Most IDE support the deployment of the build software over ssh to a target system. So a ssh and sftp server is essential for development.

Buildroot provides the SSH and SFTP server in seperate packages:

* `Target Packages -> Networking Applications -> gsftpserver`, enable the SFTP Server, for file transfers.
* `Target Packages -> Networking Applications -> dropbear`, enable the SSH Server, for a secure shell

A NTP client will also be installed, so the target system can fetch the correct time over a NTP Server.
This is needed for a successful SSH HTTP Request of ATC_Controller application to the chess ATC_Server.
With incorrect time setting, the Client/Server is not able to verify a SSL Certificate.

#### INTER PROCESS COMMUNICATION

For communication of the gui and the control software a inter process communication system is nessessary.
It uses the ZeroMQ protocol, so it is needed so install the zeromq library.

* `Target Packages -> Libraries -> Networking -> zeromq`, enable zeromq messaging library to use the ZeroMQ protocol. (GUI communication).
* `Target Packages -> Libraries -> Networking -> czmq`, client library for ZeroMQ.
* `Target Packages -> Libraries -> Crypto -> libsodium`, enables crypto functions for ZeroMQ.

For message serialization, the google protobuf project was used. Here buildroot offers the `libprotobuf`.

* `Target Packaged -> Libraries -> Others -> protobuf`, enable the protobuf library.

#### MISC PACKAGES

These packages are not required, but used for development.

* `Target Packages -> Text editors -> nano`, install a simple text editor
* `Target Packages -> Networking Applications -> rsync`, proves simple file sync (also used by QT if avariable).

There are some more applications and libraries for development and testing installed, but the system is working with these mentioned above.

#### STAT PACKAGE
In the default configuration the `stat` command is missing on the target filesystem. The command is needed in order to use the Visual GDB Plugin later for remote debugging.
It uses the command to verify a successful depoyment of the compiled binary.
The `stat` command is located in the `coreutils` package, which is part of the busybox package. Busybox offers a different configuration menu which is accessable with the `$ make busybox-menuconfig`. In the following window the package can be activated in the `Coreutils -> stat` submenu.

### FILE SYSTEM SIZE

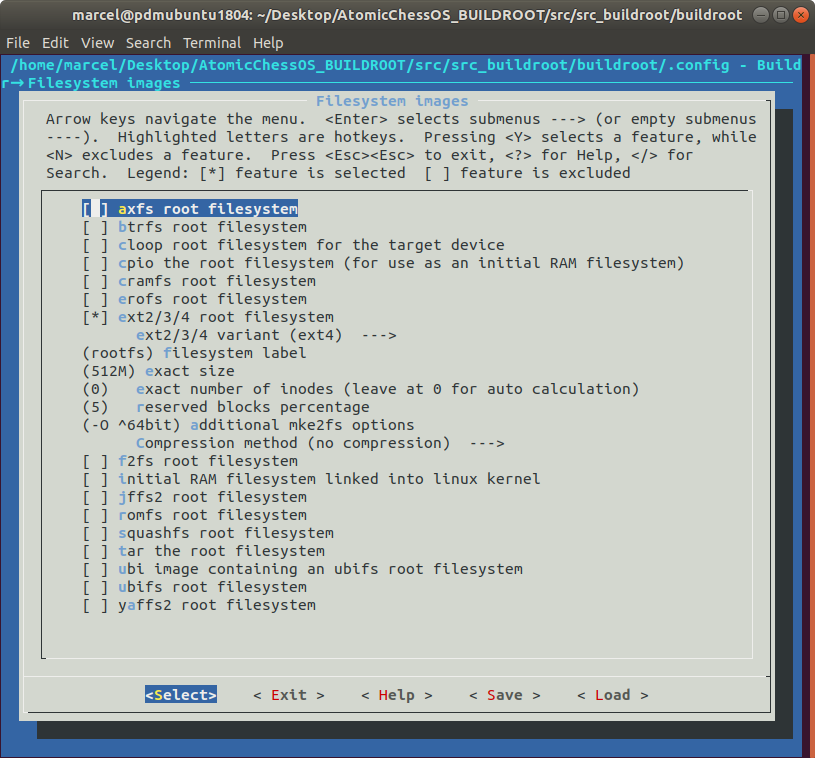
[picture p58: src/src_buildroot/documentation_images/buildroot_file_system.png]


The QT libraries and the other needed libraries are quite large in size. For the full QT5 with QT3D and the Virtual Keyboard and the nedded QuickControls II the rootfs file system is about 230MB. The default setting is 128MB. So buildroot can not build the final image beacuas its not enought space. To increase the rootfs maximum size, buildroot provides a size option under `Filesystem images -> root filesystem -> exact size`. With the `Space-Key` it is possible to edit the default value to 512M. A Zero for automatic determination is not supported.

The `Fileystem images` category, provides several other options for the rootfs. Its also possible to create a readonly filesystem or a compressed one. For debugging purposes, the readonly filesystem option is disabled. 
For deploying new versions of the image, the compression method is set to `.gz` with the option `Filesystem images -> Compressionmethod (gzip)` for a smaller rootfs partition. After a build the normal image `sdcard.img` was created, also the compressed version of the rootfs `rootfs.ext2.gz`.

All other settings are the default settings.

After building a complete image the size is about 310MB in Size, this includes the bootloader, os with all libraries and packages with the ATC needed programs (ATC_UI, ATC_Client).

### FILE SYSTEM OVERLAY
* general function and usage
* usage in buildroot to modify the final filesystem
* concrete usage here, with ssh keys
?? IMAGE OF THE OVERLAY DIAGRAM ??

#### AUTOBOOT AND LOG ROATION

All ATC applications, like the ATC_GUI and the ATC_Controller, have to start with the system automaticly.
For this purpose the linux system offers several different methods to accomplish this task.

In this case, the goal is to start the Applications as service, after the the rest of the system is booted up.
The `init.d` system offers a priority handling for startup scripts, placed inside if the `/etc/init.d` folder of the system.
The startup script has defined parameters (`start`,`stop`,`restart`) which handle the start and stop procedure of the applications to run.

The body of an `init.d` script is listed below.

```bash
#!/bin/sh
#
# atc        Starts all atc pacakges.
#
umask 077

start() {
	modprobe i2c-dev
   	/usr/ATC/atc_ui &
	/usr/ATC/atc_controller &
	printf "Starting atc: "
	touch /usr/ATC/ATC_LOCK
	echo "OK"
}
stop() {
	printf "Stopping atc: "
	killall atc_ui
	killall atc_controller
	rm -f /usr/ATC/ATC_LOCK
	echo "OK"
}
restart() {
	stop
	start
}

case "$1" in
  start)
	start
	;;
  stop)
	stop
	;;
  restart|reload)
	restart
	;;
  *)
	echo "Usage: $0 {start|stop|restart}"
	exit 1
esac
exit $?

```

The naming of the script is important. As mentioned `init.d` offers a priority system, which is defined in the name of the script.

In the case of the ATC applications the startupscript is called `/etc/init.d/S99atc`.
The naming convention is the following:

`/etc/init.d/<TYPE><PRIORITY>name`

The type charakter is `S` which stands for service.
`init.d` offers priorities from `0` to `99` and the name can be a visible name to identifiy the service.
The goal is to start the script at the end of the startup routine, so the priority of `99` is set.

A last step is reuqired. Its nessessary to make the script executable, which is possible thought the `chmod` command.

`$ sudo chmod +x ./OVERLAY_FS/etc/init.d/S99atc`, marks the the script as executable.

After rebuilding the image, the embedded system shouls start the ATC Applications automaticly, with no need for an console login.
Its also possible to start and stop the script by calling `$ /etc/init.d/S99atc {start|stop}`.

The log that the applications generated, started with `init.d` can be found in the `/var/log/<FILENAME>.log` folder, where the name matches the `init.d` filename.

##### LOG ROATION

Logrotate is a system utility that manages the automatic rotation and compression of log files.
If log files were not rotated, compressed, and periodically pruned, they could eventually consume all available disk space on a system. 
In this case we dont have much space left on the partition, one options is to simply do not log anything or redirect the logoutput to `/dev/null`.
Especially for a long term test of the running system, logs are nessessary for debugging. 

Logrotate offers two ways of configuration, the first thought the configuration file located in `/etc/logrotate.conf`.
At the start of the file, other configuration files are included located in the `/etc/logrotate.d/`

```bash
/var/log/apt/atc.log {
  rotate 10
  hourly
  missingok
  notifempty
}
```

* `rotate`, keeps 10 logfiles stored
* `hourly`, interval of the rotation, also other intervals possible `daily, monthly,..`
* `missingok`, if the application has no logfiles, logrotate will print an error. The `missingok` attribute disables this behavior.
* `notifempty`, do not create a new logfile or roate the logfile, if the logfile of the application is empty.

It is also possible to set several different other attributes like `compress`. This compresses the logfile to an `.gz` archive.

The preconfigured logrotate configuration for the ATC applications can be found in the overlay fs folder of buildroot `./OVERLAY_FS/etc/logrotate.d/atc`

Its also possible to manually reload the logrotate configuration by using the. `logrotate /etc/logrotate.conf --debug` command, which loads the configuration and displays the loaded configuration.

#### SSH KNOWN HOSTS
* using the overlay to insert a known hosts file with the already known ssh keys 

## HOW TO FINALLY BUILD

Now everything is setup, so its possible to build the image. From a fresh buildroot installation it can take serveral hours to build the image. Buildroot download the sourcefiles only once to the dowload folder `./dl`. The generated output files can be found in the output directory `./output`. This folder contains several subfolder with the build results.

The `$ make` command starts the build process.
On the development pc (Ubuntu 20.04, IntelCore i9 9900K with 24GB RAM), the a fresh build took about 2h43m.

#### CAUTION
Editing some settings can require a complete requild, for example `Kernel` and  `Target Options` settings.
To cleanup the buildroot cache and output folders, run `$ make clean`

After some time, the process output should end with `INFO: adding roofs partition; INFO: writing MBR`, so everything is finished.
The result can be found in the output directory:

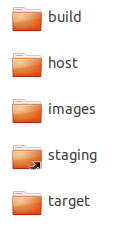
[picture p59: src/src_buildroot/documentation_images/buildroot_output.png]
OUTBUT_FOLDERS


* `build`, contains the compiled libraries and other compile software
* `host`, contains the build software for the host, including the cross compile toolchain
* `images`, contains the final sd card image
* `target`, this is a copy of the rootfs of the target device

#### TARGET BUILD RESULT

The build image can be found in `./output/images/sdcard.img`. This image already contains the root filesystem, the boot partition with bootloader and firmware espacially for the RPI.

It can be flashed using the linux `dd` command
`$ dd bs=4M if=./sdcard.img of=/dev/<SD_CARD> conv=fsync`
or by using a gui based utility like [Win32DiskImager](https://github.com/znone/Win32DiskImager) or the [Etcher](https://www.balena.io/etcher/).

After flashing the image to an sd card, the device is ready for booting.
If the device boot sequence finsihed, its possible to connect with the taerget board over SSH with the in the `System-Settings` Chapter given settings.
On the development pc its also possible to connect without a user password. This is possible though host public key signature the `/root/.ssh/known_hosts` file, given though the `FILE SYSTEM OVERLAY` system in the build process.

#### HOST CROSS COMPILER

The crosscompiler (gcc,g++,gdb, ...) can be found in the sysroot directory `./output/host/bin/`

* G++ `arm-buildroot-linux-gnueabihf-g++`
* GCC `arm-buildroot-linux-gnueabihf-gcc`
* GDB `arm-buildroot-linux-gnueabihf-gdb`
* CMAKE `cmake`
* QT_QMAKE `qmake`, if qt was selected

The sysroot of the target system (needed for the QT Kit Sysroot Setting) is located in the  `./output/host/arm-buildroot-linux-gnueabihf/sysroot` folder.

#### BUILD A SINGLE PACKAGE

For building a single package, for example to debug the buildprocess if a new created package, buildroot provedes a make command.

`$ make <PACKAGE_NAME>-rebuild`

The package name can be found in the package folder of buildroot `./packages`.
A rebuild does not downloads the source again if a fixed commit id is present in the `.mk` File of the package.
Instead the already downloaded source in `./buildroot/dl` will be used.

## ADDING OWN PACKAGES

### PACKAGE STRUCTURE
This chapter only explains the basics about creating packages. Buildroot has a very powerful packages system, which is not needed for this project.
Here also the system dependencies are not considered.

After building the first image successfully, our goal is to add custom software packages to the buildroot configuration.
All avariable pacakges definitions are located in the package directory `./packages`.
Each package is located in a seperate folder inside the `./packages` folder.
The folder is called like the package name.

The package folder contains at least two files:

* `<PACKAGE_NAME>.mk`
* `Config.in`

### PACKAGE CONFIG FILE
The `Config.in` file contains the information, that are visible on the configuration menu `make menuconfig`.

Listed below is the simplest package information, which the `Config.in` can contains:

```bash

config BR2_PACKAGE_PACKAGENAME
    bool "PACKAGENAME"
    help
        INFORMATION ABOUT THE PACKAGE

```

The first line is the start configuration for the specific package, Important is `PACKAGENAME` at the end of the line.
Followed by the bool option. This option is visible under the buildroot configuration menu.
The `help` section, can contains several information about the author / functionallity of the package.

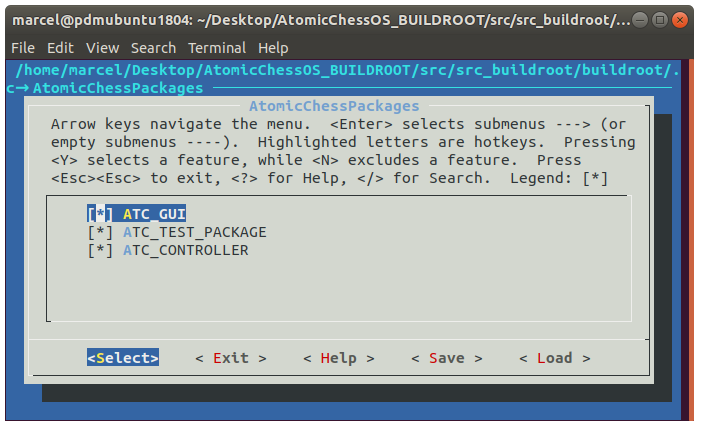
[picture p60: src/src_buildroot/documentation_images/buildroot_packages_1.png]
BUILDROOT_PACKAGE_1


### PACKAGE MAKEFILE

The `<PACKAGENAME>.mk` is the makefile or build reciepe for the package.
The file contains the build and install instruction for the package.

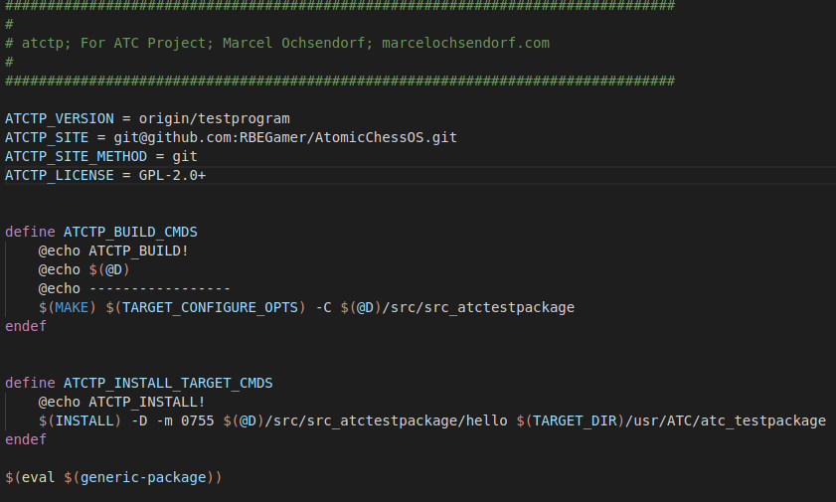
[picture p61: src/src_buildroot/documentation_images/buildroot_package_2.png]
BUILDROOT_PACKAGE_2


#### SOURCE FILE LOCATIONS
The first information, is the location of the sourcefiles of the package.
Buildroot always downloads the package sources from an other location.

Its possible to store the sources local but its not recommended, so its not explained here.
The source files of the custom packages are stored in a git repository.

* `<PACKAGESNAME>_VERSION = origin/master`, is the commitid or branch of the git repository.
* `<PACKAGESNAME>_SITE = git@github.com:RBEGamer/AtomicChessOS.git`, is the git server url
* `<PACKAGESNAME>_SITE_METHOD = git`, use git.

It is also possible to download the source as a zip or tarball archive from a webserver.
In this case the `<PACKAGESNAME>_SITE` key is the url without the filename and the `<PACKAGESNAME>_VERSION` the filename.

#### BUILD COMMANDS
Next step is the definition of the build steps.

The `define <PACKAGENAME>_BUILD_CMDS` starts a block of shell commands, which will executed during the build phase.

Buildroot defines some environment variables, for example the directory of the downloaded source or the location of the make executable.

* `$(@D)`, defines the directory of the source files
* `$(TARGET_DIR)`, defines the sysroot of the target device. Its mainly used for the installation process of the compile binaries.
* `$(MAKE)`, defines the actual make executable

Variables for compiler, qmake, cmake are also defined by buildroot, using the cross compile toolchain.

* `$(QT5_QMAKE)`, defines the QT Qmake executable
* `$(CAMKE)`, define the CMAKE executable
* `$(CC)`, defines the GCC compiler
  
The install block has to be closed with an `endef` line.

##### SITENOTE C++17

After adding more features to the ATC_GUI userinterface. The project can not be build with builroot, but manually with the QT Creator.
After investigating the error log of the make command, it turns out that the g++ compiler does not run with the C++17 option.
The ATC_GUI requires C++ Version 17 for the enum types, so in the qt projectfile `rpidisplay.pro` the c++ compiler flag was already set.

* `CONFIG += c++17 c++1z`
* `QMAKE_CXXFLAGS += -std=c++17`

These settings worked in the QtCreator environment just fine, but with the buildprocess in buildroot (qmake,make), qmake overrides the set config options in the project file.

The solution for this problem is, to define the `-std=c++17` compiler option manually in the buildroot package makefile `./packages/atcgui/atcgui.mk`.
After the modification, the buildprocess runs without a problem.

C++17Fix

##### END SITENOTE

#### INSTALL COMMANDS
After the build instructions, the install steps follows.
The installation steps in general, copies the the build results from the package, like the executables or shared libraries to the target filesystem.

The `define <PACKAGENAME>_INSTALL_TARGET_CMDS` follows the concepts as the build commands.
Here the defines become useful, especially the `$(TARGET_DIR)`.

Now the configuration of the package is complete, but if the configuration menu is opened, there is no entry with the new pacakge.
The reason for that is, that we have to tell buildroot where to show the new package in the menu.
To do this there is a configuration file located in the packages folder `./packages/Config.in`.

```bash
menu "AtomicChessPackages"
	source "package/atcgui/Config.in"
	source "package/atctp/Config.in"
	source "package/atcctl/Config.in"
endmenu
```

To add the new package to a existing menu, simply to use the source command.
The path behinf the source prefix is the relative path to the `Config.in` file of the package that should be added.

It is also possible to add new menu structures, as shown above. In this example a new entry called `AtomicChessPackages` was added with three packages inside of the menu.

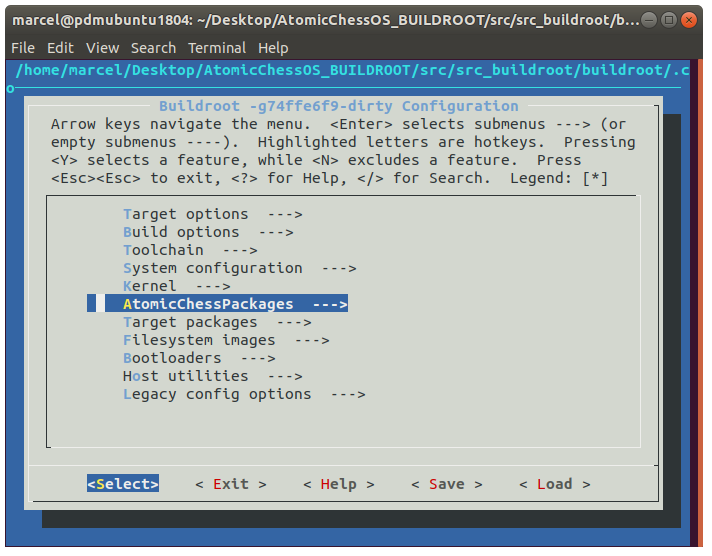
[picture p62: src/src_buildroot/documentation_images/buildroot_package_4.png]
BUILDROOT_PACKAGE_1


To test the new created package, its is also possible to build the single package by using its name, as described in the chapter `BUILD A SINGLE PACKAGE`.

## HARDWARE SUPPORT I2C SPI

The ATC Project uses the SPI bus of the Embedded System to communicate with the motor drivers. 
In addition the I2C bus is used to communicate with the nfc reader. In order to use the bus, the `i2c` kernel module has to be loaded with the `modprobe` command.

An other solution for automatic module loading, is `/boot/config.txt` file on the boot partition, but the embedded system is not loading kernel modules specified in the file. This is an issue of the integrated bootloader that buildroot builds. 
To solve this issue an option is to replace the bootloader with the original bootloader from the RaspberryPi system, but in this case, loading the module by hand or script is acceptable.

## FIRMWARE UPDATE

### UPDATE STRATEGY

#### SINGLE COPY
#### DOUBLE COPY

### ADDING A SECOND 'rootfs' partition
In order to implement the `double copy` update strategy, a third partition has to be added to the image.
The first partition is the `boot partition`, followed by the `rootfs`.
The goal is to add a third partition called `rootfsbackup` to the image.
Each board definition, contains a file `genimage.cfg`, which contains partition description.

```cfg
// board/raspberrypi3/genimage-raspberrypi3.cfg
image boot.vfat {
 ...
 ...
 ...
}
//--- CREATE EMPTY 1024MB EXT4 IMAGE
image backup.ext4 {
  ext4 {}
  size = 1024M
}
image sdcard.img {
  hdimage {
  }

  partition boot {
    partition-type = 0xC
    bootable = "true"
    image = "boot.vfat"
  }

  partition rootfs {
    partition-type = 0x83
    image = "rootfs.ext4"
    size = 1024M
  }
  //------ ADDED ROOTFSBACKUP PARTITION ------//
  partition rootfsbackup {
    partition-type = 0x83
    image = "backup.ext4" //USE CREATED EMPTY IMAGE FROM ABOVE
    size = 1024M
  }
}
```
The `rootfsbackup` was added in the file and has the same size as the `rootfs` partition. The size of `rootfs` and `rootfsbackup` was increased to 1024MB to have enought space for later

Also the partation size was increased for `rootfs` and `rootfsbackup` in the `genimage.cfg` file using the `size` attribute.

After flashing the image to an empty sd card, the partition scheme looks as the following.

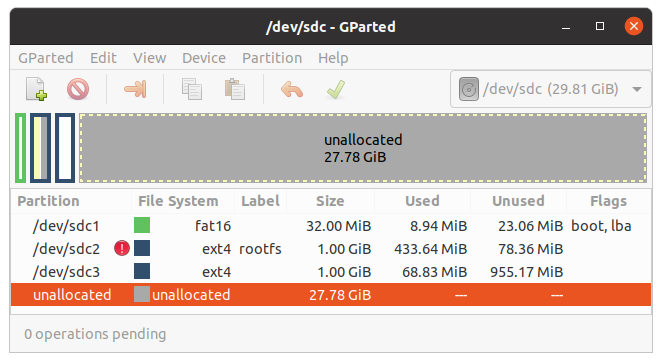
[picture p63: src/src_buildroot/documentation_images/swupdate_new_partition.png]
DUAL_COPY_PARTITION_SCHEME


### SWITCHING BETWEEN PARTITIONS
In the current boot configuration, the system boots up, mount the `rootfs` partition and continuous the startup process.
The dual copy update strategy, updates one of the two partitions alternating.
In the current setup, after updateing the `rootfsbackup` partition, the system still boots from the `rootfs` partition and the new firmwar never starts.
So a possibility is needed to swicht between both partitions.
In order to archive this functionallity, the `boot`partition comes handy.

First information is needed from which is the root partition.
A simple solution is to parse the kernels `cmdline` and get the `root=` attribute.

The easiest way is to get the current cmdline with `$ cat /proc/cmdline` or parse it directly from the `boot` partition.

```text
cat /proc/cmdline
... vc_mem.mem_size=0x40000000  root=/dev/mmcblk0p2 rootwait console=tty1 console=ttyAMA0,115200
```

Finally parse the `root` attribute.
```bash
$ cat /proc/cmdline | sed -e 's/^.*root=//' -e 's/ .*$//'
$ /dev/mmcblk0p2
```

Also we need to modifiy the `cmdline` in order to change the `root` attribute to the new root partition. 
This can be archived with mounting the `root` partition into a folder.

On the target device the partitions can be found in the `/dev` folder:

* `/dev/mmcblk0p1` -> `boot` partition
* `/dev/mmcblk0p2` ->`rootfs` partation
* `/dev/mmcblk0p3` -> `rootfsbackup` partition

With the mount command a parition can be mounted to a specified folder.
In this example the goal is to mount the `boot` partition into a folder called `boot`
`$ mkdir /boot && mount /dev/mmcblk0p1 /boot`.

* startup
*

In the current boot configuration

### SWUPDATE

* update methods
* update strategie single dual copy
*

`swupdate` is already avariable as package in buildroot:

* `Target Packages ->System tools -> swupdate`, enable swupdate package.

Also a few support-packages are needed to automate the update process:

* `Target Packages ->Filesystem and flash utilities -> e2fsprogs`, to check the updated filesystem for errors.
* `Target Packages ->Libraries -> JSON/XML -> libjson`, json support for communicating with hawkbit server.
* `Target Packages ->Libraries -> JSON/XML -> json-c`
* `Target Packages ->Libraries -> Networking -> libcurl`, for swupdate download feature.

The `swupdate` package offers a more advanced configuration menu. In after selecting the `swupdate` package only the basic configuration is set by default.
For this project, a update using a local webserver or using a `hawkBit` server is a good way to updating over a remote server, with no need for a USB drive.

`$ make swupdate-menuconfig`, open the menu and the following changes were made:

* `Swupdate Configuration -> Enable image downloading`, enables downloading of updates from a webserver.
* `Swupdate Configuration -> Web Server`, enables downloading of updates from a webserver.
* `Swupdate Configuration -> Enable verification of signed images`, enables signed updates.
* `Swupdate Configuration -> Scricatta -> Server ->Server Type (hawkBit)`, enables automated rollout using a `hawkBit` server.

All changes after selecting `<SAVE>` will be discarded, to save the changes permanently in the `.config` file, the `$ make swupdate-update-defconfig` command has to be executed.
After rebuilding the image with `$ make` or using the build script `$ ./build.sh`, the `swupdate` command is avariable on the target.
The one of simplest methods of using `swupdate` is to start a webserver, where a update package can be uploaded.

`$ swupdate -v -w "--document-root /var/www/swupdate --port 8081"`, which start the webserver on port `8081`.

On the target system, the `swupdate` starts automatically by using the previously described `init.d` method.
For this reason a script `OVERLAY_FS/etc/init.d/S88swupdate` was created, which starts the `swupdate` webserver and the `hawkBit` client which is integrated in `swupdate`.

#### UPDATE PACKAGE CREATION

```cfg
software =
{
        version = "VERSION";
        rootfs:
        {
        	images: (
                {
                        filename = "rootfs.ext2.gz";
                        device = "/dev/mmcblk0p2";
                        type = "raw";
                        sha256 = "RFSHASH";
                        compressed = true;
                }
        	);
        };
        rootfsbackup:
        {
        	images: (
                {
                        filename = "rootfs.ext2.gz";
                        device = "/dev/mmcblk0p3";
                        type = "raw";
                        sha256 = "RFSHASH";
                        compressed = true;
                }
        	);
        };
}
```

#### HAWKBIT CONFIGURATION
In order to use the `hawkBit` client, `swupdate` can be configurated with an additional configuration file, located in `./OVERLAY_FS/etc/swupdate/swupdate.cfg`.
The config file contains the configuration for the `hawkBit` client.
The essentials detailes in the config file, is the `id` of the device and the `url` to the `hawkBit` server.

```cfg
// /etc/swupdate/swupdate_template.cfg
...
...
suricatta :
{
	tenant = "default";
	id = "ATCTABLE"; //DEVICE ID
	url = "http://192.168.178.125:8082"; //hawkBit Server URL
	nocheckcert	= true;
	enable		= true;
};
```
The `id` should be unique for every device. For easy setup the unique mac adress for the ethernet interface `eth0` on the target was used for this id.
To simplify the process a script `OVERLAY_FS/etc/swupdate/create_swupdate_cfg.sh` was created to automaticly replace the `id` with the mac adress at system startup. A template configuration `swupdate_template.cfg` in addition with the `sed` command to replace the placeholder `ATCTABLE` with the mac adress.

```bash
#!/bin/sh
# /etc/swupdate/create_swupdate_cfg.sh
#GET MAC ADDRESS
HWID=$(cat /sys/class/net/eth0/address)
#REMOVE THE : OF THE MAC ADDRESS TO GET A CLEANED ONE
HWIDCLEANED=${HWID//:/}
cp /etc/swupdate/swupdate_template.cfg /etc/swupdate/swupdate.cfg
sed -i 's|DEVICEID|'"$DEVICEID"'|g' /etc/swupdate/swupdate.cfg
```

With this method its simple to deploy one image, to serveral different devices, and the device setup itself automaticly.
Now the configuration is compl

### HAWKBIT
` $ sudo docker run -itd -p 8082:8080 --restart always hawkbit/hawkbit-update-server:latest --hawkbit.dmf.rabbitmq.enabled=false --hawkbit.server.ddi.security.authentication.anonymous.enabled=true`

To open the configuration website, navigate to `http://<IP>:8082/` with username `admin` and password `admin`.

## PREPERATION WORK FOR CI

At this point the whole buildroot setup is working on our development machine.
The final goal of the installation is, to automate the build process further more using a continous integtation (CI) system like jenkins.
To make the integration into the CI system easier, a single bash file was created to handle all for a build nessessary commands.
The file is placed in the buildroot-root directory `./build.sh` and invokes the make comand in order to run a buildroot build.

On step is important before make can be called. After a fresh download of the buildroot directory from the git server, it is not possible to directy call make. The `.config` file will not be synchronizes by the `.gitignore` file, so the file is missing in the buildroot-root directory.
To solve this issue, the buildroot configuration is stored under a different file name `./config_backup`. The `build.sh` file copies the `config_backup` to `.config`, and invoke the make command sucessfully.

Later the CI system simply have to call the `build.sh` file in order to start the build complete process.

In addition, later its also possible to add new features to the `build.sh`. For example to upload the final image to an FTP Server.

## CONCLUSION BUILDROOT
The configuration of the buildroot system was a bit difficult. 
There are a few dependencies eg for the touchscreen which have to be checked manually.
The goal of the buildroot system for the ATC Project is, to build a working/ ready to use image, which contains all needed software to drive a ATC Table.

For this purpose, three custom buildroot packages were created, to intregrate the needed ATC Software into the final SD-Card image.
The final SD Card image, can directly flashed to the RaspberryPi and the build cross plattform compiler toolchain can be used to develop software on the host computer and run it on the target hardware.

This setup was used in the whole software development process. Especially for the gui application. QT5 needs this cross compile toolchain to compile the application successful.

In summary buildroot was a great choice to work with. The process of integration of own packages was straight forward. In the end building an linux image for an embedded device that simply works, including all needed software for the project is very great.
This system also has advantages as not every image has to be adjusted manually, especially if the number of embedded systems to be installed increases.

??
The now created configuration and patching of buildroot allowes delivers a complete running system for QT and Hardware apllications.
The system is very easy to use, by simply calling the `./build.sh` script and flashing the `sdcard.img` file to an sdcard.
The RaspberryPi boots with ssh server, configures I2C and SPI and boots up the ATC software services.

??

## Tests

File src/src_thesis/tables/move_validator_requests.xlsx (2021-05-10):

AtomicChess Move-Validator Service API | API-Route | Method | Form-Data
Check Move | /rest/check_move | POST | fen, move, player
Execute Move | /rest/execute_move | POST | fen, move
Validate Board | /rest/validate_board | POST | fen
Init Board | /rest/init_board | GET

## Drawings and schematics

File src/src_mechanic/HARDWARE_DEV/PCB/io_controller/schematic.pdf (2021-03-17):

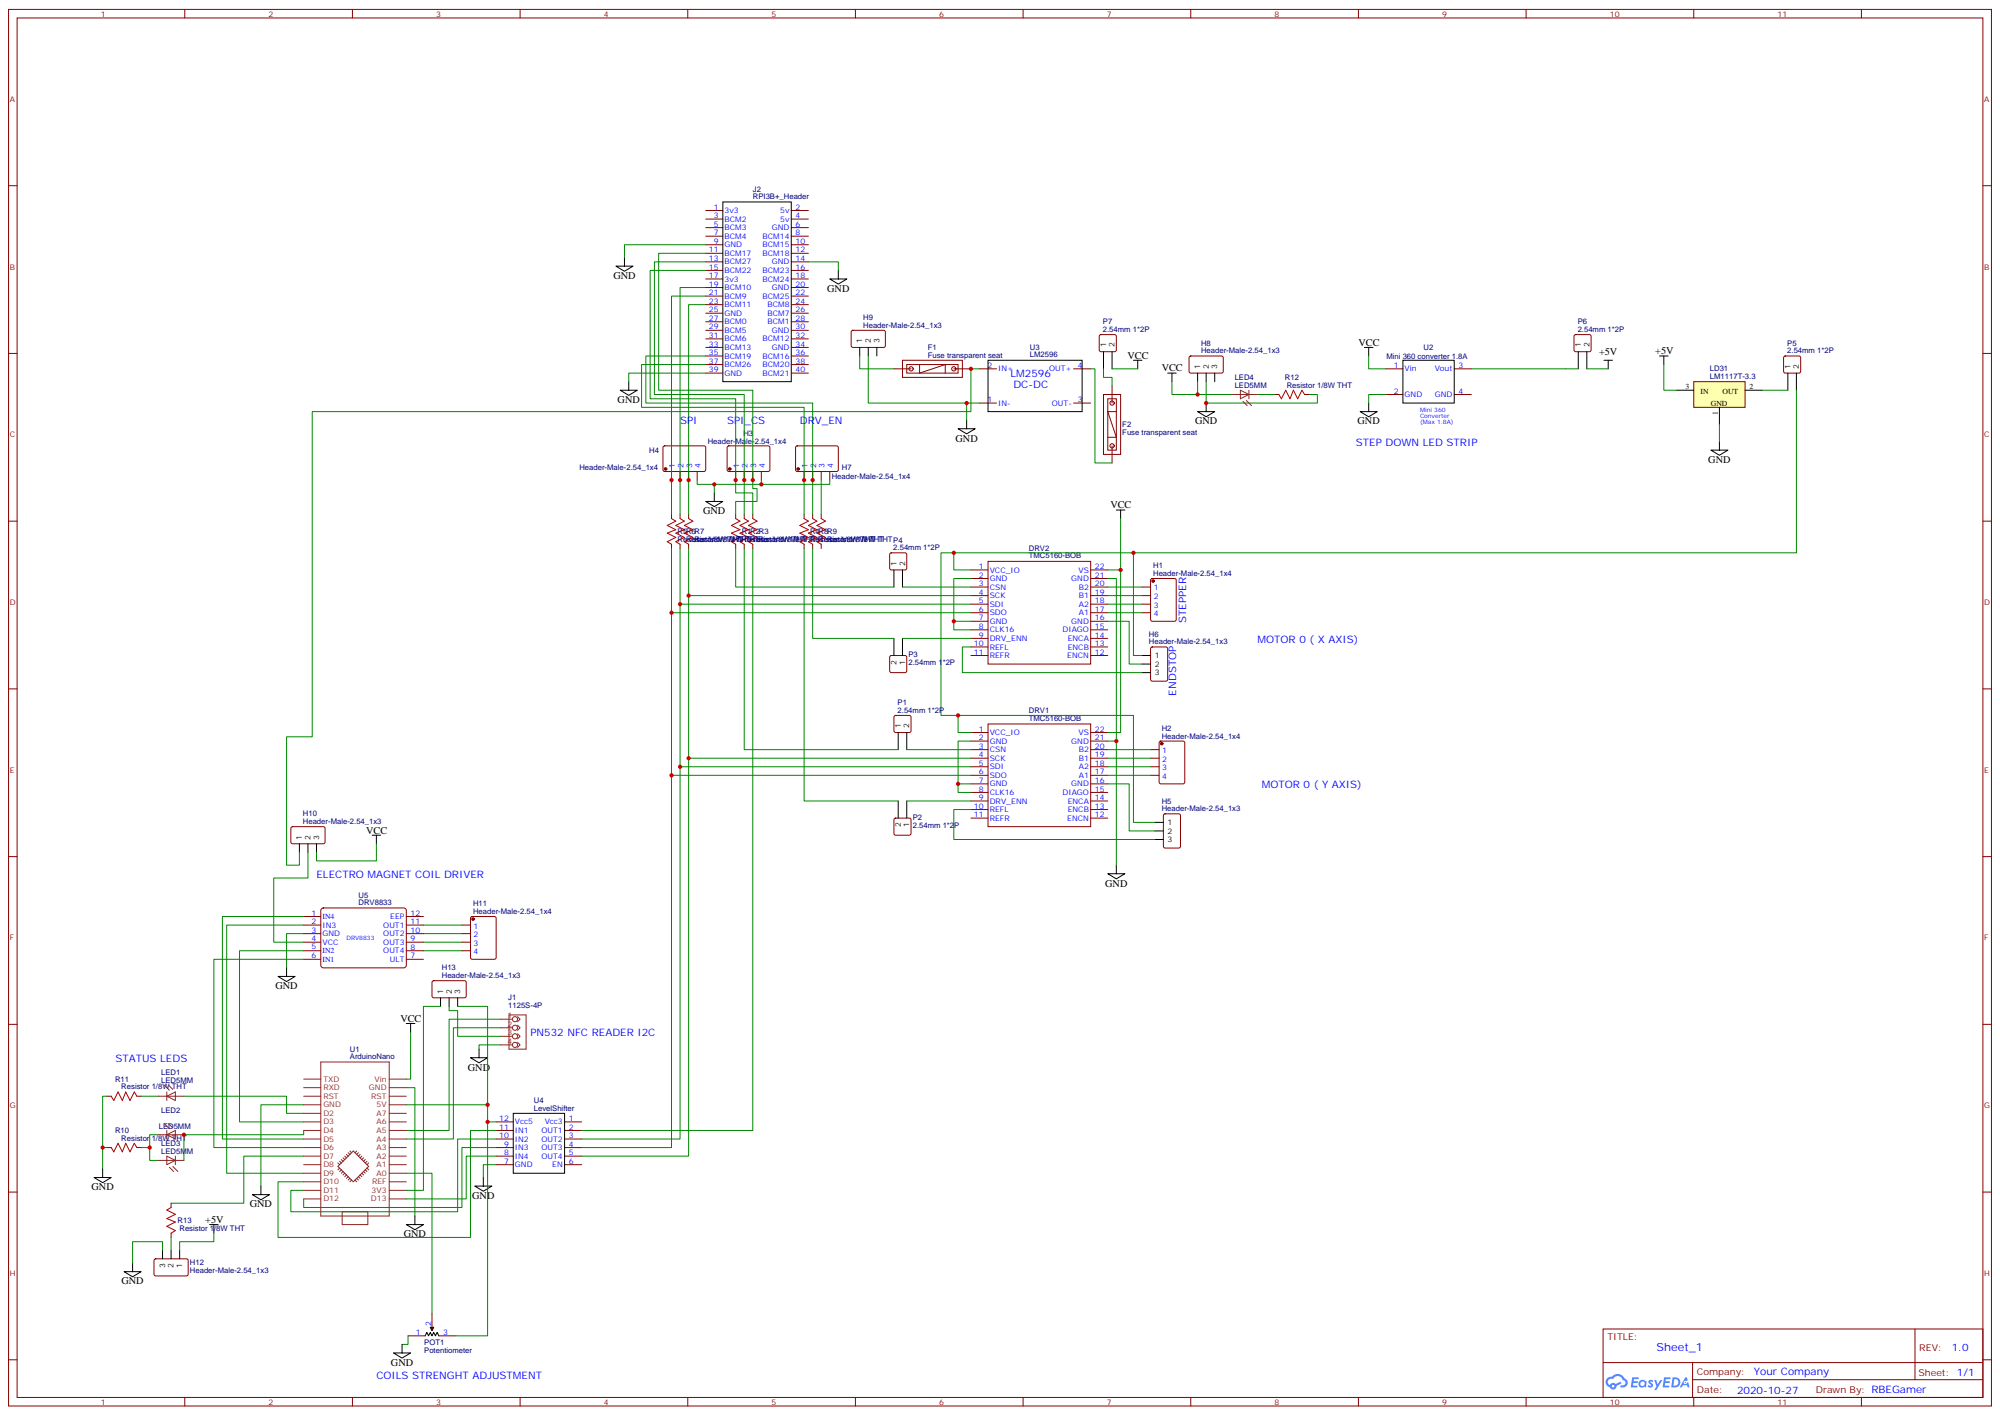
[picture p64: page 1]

GND
STEP DOWN LED STRIP

ELECTRO MAGNET COIL DRIVER

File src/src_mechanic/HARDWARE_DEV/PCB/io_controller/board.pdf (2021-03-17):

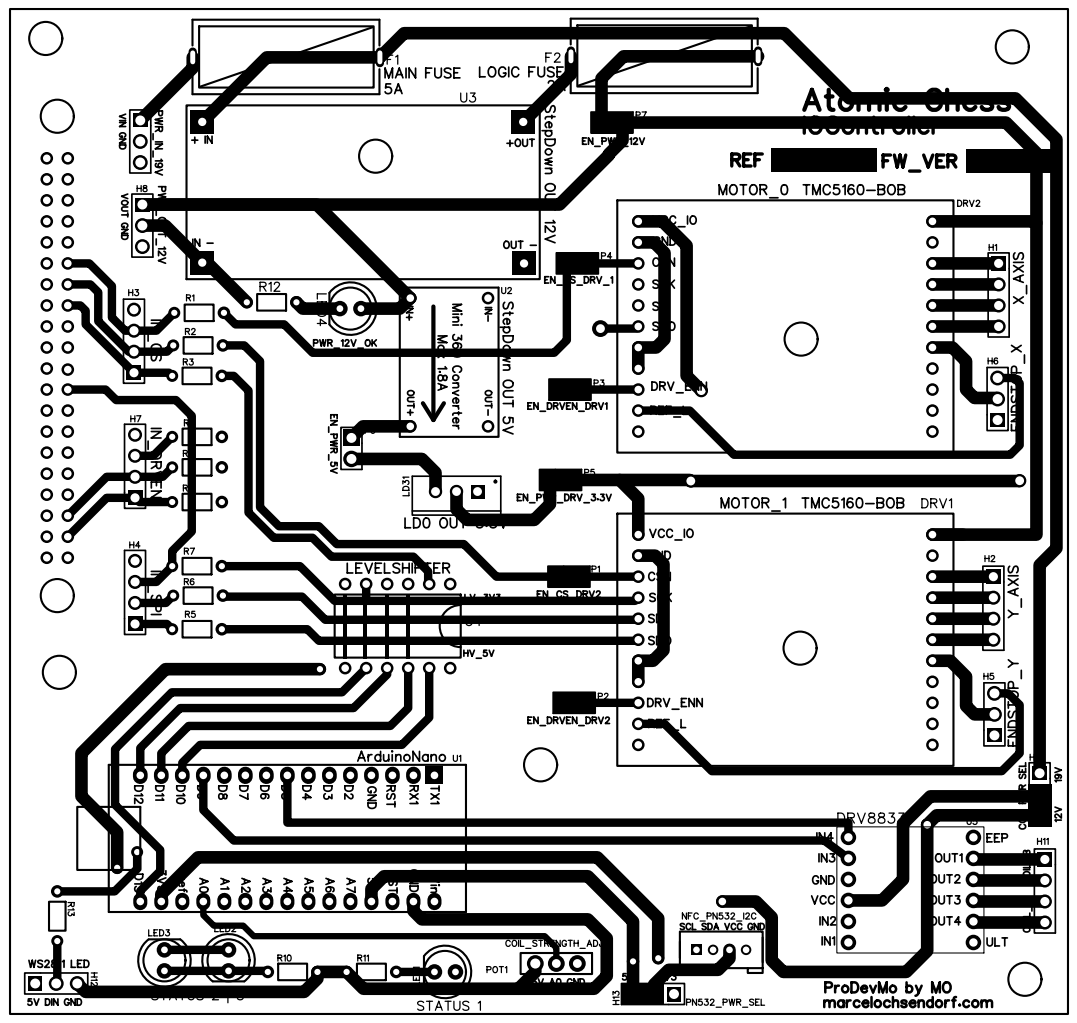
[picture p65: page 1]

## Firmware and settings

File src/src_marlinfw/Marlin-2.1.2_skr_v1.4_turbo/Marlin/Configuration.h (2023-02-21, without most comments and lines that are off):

#pragma once
#define CONFIGURATION_H_VERSION 02010200
#define STRING_CONFIG_H_AUTHOR "Atomicchess SKR" // Who made the changes.
#define SHOW_BOOTSCREEN
  #define MOTHERBOARD BOARD_BTT_SKR_V1_4_TURBO
#define SERIAL_PORT -1
#define BAUDRATE 9600
#define X_DRIVER_TYPE  A4988
#define Y_DRIVER_TYPE  A4988
#define Z_DRIVER_TYPE  A4988
#define E0_DRIVER_TYPE A4988
#define EXTRUDERS 1
#define DEFAULT_NOMINAL_FILAMENT_DIA 1.75
#define TEMP_SENSOR_0 998
#define TEMP_SENSOR_1 0
#define TEMP_SENSOR_2 0
#define TEMP_SENSOR_3 0
#define TEMP_SENSOR_4 0
#define TEMP_SENSOR_5 0
#define TEMP_SENSOR_6 0
#define TEMP_SENSOR_7 0
#define TEMP_SENSOR_BED 0
#define TEMP_SENSOR_PROBE 0
#define TEMP_SENSOR_CHAMBER 0
#define TEMP_SENSOR_COOLER 0
#define TEMP_SENSOR_BOARD 0
#define TEMP_SENSOR_REDUNDANT 0
#define DUMMY_THERMISTOR_998_VALUE  25
#define DUMMY_THERMISTOR_999_VALUE 100
#if TEMP_SENSOR_IS_MAX_TC(0)
  #define MAX31865_SENSOR_OHMS_0      100 // (Ω) Typically 100 or 1000 (PT100 or PT1000)
  #define MAX31865_CALIBRATION_OHMS_0 430 // (Ω) Typically 430 for Adafruit PT100; 4300 for Adafruit PT1000
#endif
#if TEMP_SENSOR_IS_MAX_TC(1)
  #define MAX31865_SENSOR_OHMS_1      100
  #define MAX31865_CALIBRATION_OHMS_1 430
#endif
#if TEMP_SENSOR_IS_MAX_TC(2)
  #define MAX31865_SENSOR_OHMS_2      100
  #define MAX31865_CALIBRATION_OHMS_2 430
#endif
#if HAS_E_TEMP_SENSOR
  #define TEMP_RESIDENCY_TIME         10  // (seconds) Time to wait for hotend to "settle" in M109
  #define TEMP_WINDOW                  1  // (°C) Temperature proximity for the "temperature reached" timer
  #define TEMP_HYSTERESIS              3  // (°C) Temperature proximity considered "close enough" to the target
#endif
#if TEMP_SENSOR_BED
  #define TEMP_BED_RESIDENCY_TIME     10  // (seconds) Time to wait for bed to "settle" in M190
  #define TEMP_BED_WINDOW              1  // (°C) Temperature proximity for the "temperature reached" timer
  #define TEMP_BED_HYSTERESIS          3  // (°C) Temperature proximity considered "close enough" to the target
#endif
#if TEMP_SENSOR_CHAMBER
  #define TEMP_CHAMBER_RESIDENCY_TIME 10  // (seconds) Time to wait for chamber to "settle" in M191
  #define TEMP_CHAMBER_WINDOW          1  // (°C) Temperature proximity for the "temperature reached" timer
  #define TEMP_CHAMBER_HYSTERESIS      3  // (°C) Temperature proximity considered "close enough" to the target
#endif
#if TEMP_SENSOR_REDUNDANT
  #define TEMP_SENSOR_REDUNDANT_SOURCE    E1  // The sensor that will provide the redundant reading.
  #define TEMP_SENSOR_REDUNDANT_TARGET    E0  // The sensor that we are providing a redundant reading for.
  #define TEMP_SENSOR_REDUNDANT_MAX_DIFF  10  // (°C) Temperature difference that will trigger a print abort.
#endif
#define HEATER_0_MINTEMP   5
#define HEATER_1_MINTEMP   5
#define HEATER_2_MINTEMP   5
#define HEATER_3_MINTEMP   5
#define HEATER_4_MINTEMP   5
#define HEATER_5_MINTEMP   5
#define HEATER_6_MINTEMP   5
#define HEATER_7_MINTEMP   5
#define BED_MINTEMP        5
#define CHAMBER_MINTEMP    5
#define HEATER_0_MAXTEMP 275
#define HEATER_1_MAXTEMP 275
#define HEATER_2_MAXTEMP 275
#define HEATER_3_MAXTEMP 275
#define HEATER_4_MAXTEMP 275
#define HEATER_5_MAXTEMP 275
#define HEATER_6_MAXTEMP 275
#define HEATER_7_MAXTEMP 275
#define BED_MAXTEMP      150
#define CHAMBER_MAXTEMP  60
#define HOTEND_OVERSHOOT 15   // (°C) Forbid temperatures over MAXTEMP - OVERSHOOT
#define BED_OVERSHOOT    10   // (°C) Forbid temperatures over MAXTEMP - OVERSHOOT
#define COOLER_OVERSHOOT  2   // (°C) Forbid temperatures closer than OVERSHOOT
#define PIDTEMP          // See the PID Tuning Guide at https://reprap.org/wiki/PID_Tuning
#define BANG_MAX 255     // Limits current to nozzle while in bang-bang mode; 255=full current
#define PID_MAX BANG_MAX // Limits current to nozzle while PID is active (see PID_FUNCTIONAL_RANGE below); 255=full current
#define PID_K1 0.95      // Smoothing factor within any PID loop
    #define DEFAULT_Kp  22.20
    #define DEFAULT_Ki   1.08
    #define DEFAULT_Kd 114.00
#define MAX_BED_POWER 255 // limits duty cycle to bed; 255=full current
#define MAX_CHAMBER_POWER 255 // limits duty cycle to chamber heater; 255=full current
  #define PID_FUNCTIONAL_RANGE 10 // If the temperature difference between the target temperature and the actual temperature
#define PREVENT_COLD_EXTRUSION
#define EXTRUDE_MINTEMP 170
#define PREVENT_LENGTHY_EXTRUDE
#define EXTRUDE_MAXLENGTH 200
#define THERMAL_PROTECTION_HOTENDS // Enable thermal protection for all extruders
#define THERMAL_PROTECTION_BED     // Enable thermal protection for the heated bed
#define THERMAL_PROTECTION_CHAMBER // Enable thermal protection for the heated chamber
#define THERMAL_PROTECTION_COOLER  // Enable thermal protection for the laser cooling
#define COREYX
#define USE_XMIN_PLUG
#define USE_YMIN_PLUG
#define USE_ZMIN_PLUG
#define ENDSTOPPULLUPS
#define X_MIN_ENDSTOP_INVERTING true // Set to true to invert the logic of the endstop.
#define Y_MIN_ENDSTOP_INVERTING true // Set to true to invert the logic of the endstop.
#define Z_MIN_ENDSTOP_INVERTING false // Set to true to invert the logic of the endstop.
#define I_MIN_ENDSTOP_INVERTING false // Set to true to invert the logic of the endstop.
#define J_MIN_ENDSTOP_INVERTING false // Set to true to invert the logic of the endstop.
#define K_MIN_ENDSTOP_INVERTING false // Set to true to invert the logic of the endstop.
#define U_MIN_ENDSTOP_INVERTING false // Set to true to invert the logic of the endstop.
#define V_MIN_ENDSTOP_INVERTING false // Set to true to invert the logic of the endstop.
#define W_MIN_ENDSTOP_INVERTING false // Set to true to invert the logic of the endstop.
#define X_MAX_ENDSTOP_INVERTING false // Set to true to invert the logic of the endstop.
#define Y_MAX_ENDSTOP_INVERTING false // Set to true to invert the logic of the endstop.
#define Z_MAX_ENDSTOP_INVERTING false // Set to true to invert the logic of the endstop.
#define I_MAX_ENDSTOP_INVERTING false // Set to true to invert the logic of the endstop.
#define J_MAX_ENDSTOP_INVERTING false // Set to true to invert the logic of the endstop.
#define K_MAX_ENDSTOP_INVERTING false // Set to true to invert the logic of the endstop.
#define U_MAX_ENDSTOP_INVERTING false // Set to true to invert the logic of the endstop.
#define V_MAX_ENDSTOP_INVERTING false // Set to true to invert the logic of the endstop.
#define W_MAX_ENDSTOP_INVERTING false // Set to true to invert the logic of the endstop.
#define Z_MIN_PROBE_ENDSTOP_INVERTING false // Set to true to invert the logic of the probe.
#define DEFAULT_AXIS_STEPS_PER_UNIT   { 100, 100, 400, 96 }
#define DEFAULT_MAX_FEEDRATE          { 50, 50, 5, 25 }
#define DEFAULT_MAX_ACCELERATION      { 70, 70, 70, 10000 }
#define DEFAULT_ACCELERATION          100    // X, Y, Z and E acceleration for printing moves
#define DEFAULT_RETRACT_ACCELERATION  100    // E acceleration for retracts
#define DEFAULT_TRAVEL_ACCELERATION   100    // X, Y, Z acceleration for travel (non printing) moves
#define DEFAULT_EJERK    5.0  // May be used by Linear Advance
  #define JUNCTION_DEVIATION_MM 0.013 // (mm) Distance from real junction edge
  #define JD_HANDLE_SMALL_SEGMENTS    // Use curvature estimation instead of just the junction angle
#define Z_MIN_PROBE_USES_Z_MIN_ENDSTOP_PIN
#define NOZZLE_TO_PROBE_OFFSET { 10, 10, 0 }
#define PROBING_MARGIN 10
#define XY_PROBE_FEEDRATE (133*60)
#define Z_PROBE_FEEDRATE_FAST (4*60)
#define Z_PROBE_FEEDRATE_SLOW (Z_PROBE_FEEDRATE_FAST / 2)
#define Z_CLEARANCE_DEPLOY_PROBE   10 // Z Clearance for Deploy/Stow
#define Z_CLEARANCE_BETWEEN_PROBES  5 // Z Clearance between probe points
#define Z_CLEARANCE_MULTI_PROBE     5 // Z Clearance between multiple probes
#define Z_PROBE_LOW_POINT          -2 // Farthest distance below the trigger-point to go before stopping
#define Z_PROBE_OFFSET_RANGE_MIN -20
#define Z_PROBE_OFFSET_RANGE_MAX 20
#define X_ENABLE_ON 0
#define Y_ENABLE_ON 0
#define Z_ENABLE_ON 0
#define E_ENABLE_ON 0 // For all extruders
#define DISABLE_X false
#define DISABLE_Y false
#define DISABLE_Z false
#define DISABLE_E false             // Disable the extruder when not stepping
#define DISABLE_INACTIVE_EXTRUDER   // Keep only the active extruder enabled
#define INVERT_X_DIR false
#define INVERT_Y_DIR true
#define INVERT_Z_DIR false
#define INVERT_E0_DIR false
#define INVERT_E1_DIR false
#define INVERT_E2_DIR false
#define INVERT_E3_DIR false
#define INVERT_E4_DIR false
#define INVERT_E5_DIR false
#define INVERT_E6_DIR false
#define INVERT_E7_DIR false
#define X_HOME_DIR -1
#define Y_HOME_DIR -1
#define Z_HOME_DIR -1
#define X_BED_SIZE 700
#define Y_BED_SIZE 700
#define X_MIN_POS 0
#define Y_MIN_POS 0
#define Z_MIN_POS 0
#define X_MAX_POS X_BED_SIZE
#define Y_MAX_POS Y_BED_SIZE
#define Z_MAX_POS 200
#define MIN_SOFTWARE_ENDSTOPS
  #define MIN_SOFTWARE_ENDSTOP_X
  #define MIN_SOFTWARE_ENDSTOP_Y
  #define MIN_SOFTWARE_ENDSTOP_Z
  #define MIN_SOFTWARE_ENDSTOP_I
  #define MIN_SOFTWARE_ENDSTOP_J
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

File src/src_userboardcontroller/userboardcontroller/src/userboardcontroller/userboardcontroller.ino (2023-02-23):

// ATC PROJECT
// MARCEL OCHSENDORF marcelochsendorf.com 


/*
 * COMMANDS:
 * 
 * _coil_0_ => ALL OFF
 * _coil_1_ => A ON
 * _coil_2_ => B ON
 * _coil_3_ => A AND B ON
 * => _coil_res_ok_
 * 
 * 
 * _readnfc_ => _readnfc_res_R_ok_ OR _readnfc_res_R_notagpresent_
 * _version_ => _version_res_1.04_
 * _state_ => _state_res_ok_
 * 
 * _led_<0-5>_ => _led_res_ok_
 * 
 * _servo_<0-255>_ => _servo_res_ok_
 */



#define UBC_COMMAND_VERSION "version"
#define UBC_COMMAND_READNFC "readnfc"
#define UBC_COMMAND_STATE "state"
#define UBC_COMMAND_LED "led"
#define UBC_COMMAND_SERVO "servo"
#define UBC_COMMAND_HSV "hsv"
#include <Servo.h>
const int servo_pin = 8;
Servo myservo;

#include <Wire.h>

int pos = 0;



#include <PN532.h>
#include <NfcAdapter.h>

#include "PN532_HSU.h"
PN532_HSU pn532(Serial2);



NfcAdapter nfc = NfcAdapter(pn532);


#include "Adafruit_NeoPixel.h"
#define NUMPIXELS 120
#define NEOPIXEL_STRIP_PIN 5  

//#ifdef ARDUINO_AVR_MEGA2560
//Adafruit_NeoPixel pixels(NUMPIXELS, NEOPIXEL_STRIP_PIN, NEO_GRB + NEO_KHZ800);
//#else
Adafruit_NeoPixel pixels(NUMPIXELS, NEOPIXEL_STRIP_PIN, NEO_RGB + NEO_KHZ800);



#define MAX_COLORS 6
const byte LED_STRIP_COLORS[MAX_COLORS] = {240,180,140,90,35, 0}; //LED STRIP COLORS OFF, IDLE, WHITE_TURN, BLACK_TURN, PROCESSING



//GET A COLOR FROM THE HSV WHEEL
//SEE ADAFRUIT_NEOPIXEL LIB EXAMPLE FOR THE FUNTION
uint32_t Wheel(byte WheelPos) {
  if (WheelPos < 85) {
    return pixels.Color(WheelPos * 3, 255 - WheelPos * 3, 0);
  } else if (WheelPos < 170) {
    WheelPos -= 85;
    return pixels.Color(255 - WheelPos * 3, 0, WheelPos * 3);
  } else {
    WheelPos -= 170;
    return pixels.Color(0, WheelPos * 3, 255 - WheelPos * 3);
  }
}




byte current_led_pos = 0;

void set_neopixel(const byte _pos){
  int target_led_pos = 0;
  //GET THE COLOR FROM PREDEFINED COLOR ARRAY ELSE GET ANY COLOR...
  if(_pos >= 0 && _pos < MAX_COLORS){
    target_led_pos = LED_STRIP_COLORS[_pos];
   }
   //HOW MANY STEPS TO REACH THE TARGET COLOR
   const int steps = abs(target_led_pos - current_led_pos); 
  if(steps == 0){
    for(int i=0; i<NUMPIXELS; i++) { 
      pixels.setPixelColor(i, Wheel(current_led_pos)); 
    }
    pixels.show();
  }
   //MAKE STEPS IN WHICH DIRECTORY OF THE COLOR WHEEL
   int step_dir = 1;
   if(target_led_pos < current_led_pos){
      step_dir = -1;
    }
    
  
  for(int j =0; j<steps; j++) { 
    //INC DEC CURRENT LED POS +-1 TO GET CLOSER TO TARGET COLOR
    current_led_pos += step_dir; 
   //SET ALL PIXELS TO THE NEW STEP COLOR
    for(int i=0; i<NUMPIXELS; i++) { 
      pixels.setPixelColor(i, Wheel(current_led_pos)); 
    }
  
  pixels.show(); //SHOW PIXELS
  delay(5*(255/steps)); //WAIT SOME TIME BUT MAX 5*255ms FOR A FULL COLOR ROTATION
  }

}

void set_neopixel_hsv(const byte _hsv){
 
   //HOW MANY STEPS TO REACH THE TARGET COLOR
   const int steps = abs(_hsv - current_led_pos); 
  if(steps == 0){
    for(int i=0; i<NUMPIXELS; i++) { 
      pixels.setPixelColor(i, Wheel(current_led_pos)); 
    }
    pixels.show();
  }
   //MAKE STEPS IN WHICH DIRECTORY OF THE COLOR WHEEL
   int step_dir = 1;
   if(_hsv < current_led_pos){
      step_dir = -1;
    }
    
  
  for(int j =0; j<steps; j++) { 
    //INC DEC CURRENT LED POS +-1 TO GET CLOSER TO TARGET COLOR
    current_led_pos += step_dir; 
   //SET ALL PIXELS TO THE NEW STEP COLOR
    for(int i=0; i<NUMPIXELS; i++) { 
      pixels.setPixelColor(i, Wheel(current_led_pos)); 
    }
  
  pixels.show(); //SHOW PIXELS
  delay(5*(255/steps)); //WAIT SOME TIME BUT MAX 5*255ms FOR A FULL COLOR ROTATION
  }

}



String readString;
String getValue(String data, char separator, int index) {
  int found = 0;
  int strIndex[] = {
    0,
    -1
  };
  int maxIndex = data.length() - 1;
  for (int i = 0; i <= maxIndex && found <= index; i++) {
    if (data.charAt(i) == separator || i == maxIndex) {
      found++;
      strIndex[0] = strIndex[1] + 1;
      strIndex[1] = (i == maxIndex) ? i + 1 : i;
    }
  }
  return found > index ? data.substring(strIndex[0], strIndex[1]) : "";
}



char scan_nfc_read_error = 0;
char scan_nfc_tag(){
  scan_nfc_read_error = 0;
    if (nfc.tagPresent())
    {
        NfcTag tag = nfc.read();
      //  tag.print();
        NdefMessage  msg = tag.getNdefMessage();
        if(msg.getRecordCount() > 0){
         NdefRecord  record = msg.getRecord(0);
         int payloadLength = record.getPayloadLength();
          byte payload[payloadLength];
          record.getPayload(payload);
          String payloadAsString = "";
          for (int c = 0; c < payloadLength; c++) {
          payloadAsString += (char)payload[c];
     
          }
          
          //Serial.println(payloadAsString);
          int index_equal =payloadAsString.indexOf("="); //GET FIRST = charakter which is the start of the payload
          //CHECK IF = EXISTS AND LENGHT IS HIGHER  =<ID>=
          if(index_equal >= 0 && payloadLength > index_equal+1){
            char id = payloadAsString[index_equal+1];
            //Serial.println(id);
          return id;
          }
          
         return 0;
         scan_nfc_read_error = 1;
         }

         return 0;
        scan_nfc_read_error = 2;
    }

    //NO TAG PRESENT
    scan_nfc_read_error = 3;
  }


const int STATE_LED = 4;






void setup(void) {
  pinMode(STATE_LED, OUTPUT);

  
  
  //Serial.println("_ENTERSETUP_");

  pixels.begin();
  pixels.clear();
  pixels.show();
  
  Wire.begin();
  Wire.setClock(80000L);
  nfc.begin();


  
  set_neopixel(MAX_COLORS-1);

  //INIT SERIAL AT THE END: SO NO MESSAGES FROM THE NFC LIB WILL BE DELIVERED
  Serial.begin(9600);


  myservo.attach(8); 
  myservo.write(100);              // tell servo to go to position in variable 'pos'

}


void loop() {
 

  while (Serial.available()) {
    delay(30); //delay to allow buffer to fill
    if (Serial.available() > 0) {
      char c = Serial.read(); //gets one byte from serial buffer
      readString += c; //makes the string readString
      if (c == '\n') {
        Serial.flush();
        break;
      }
    }
  }

if (readString.length() > 0) {

 // digitalWrite(STATE_LED,HIGH);
  
  
  if (getValue(readString, '_', 1) == UBC_COMMAND_READNFC) {

   const char readres = scan_nfc_tag();
   String error_code = "ok";
   if(scan_nfc_read_error != 3 && scan_nfc_read_error != 0){
    error_code = "readerror";
   }else if(scan_nfc_read_error == 3){
       error_code = "notagpresent";
   }
    //scan_nfc_read_error = 3 // NO TAG PRESENT
    Serial.print("_readnfc_res_" + String(readres) + "_" + error_code + "_\n");
   

  } else if (getValue(readString, '_', 1) == UBC_COMMAND_STATE) {
     Serial.println("_state_res_ok_");
  }else if (getValue(readString, '_', 1) == UBC_COMMAND_VERSION) {
     Serial.println("_version_res_2.04_");
  }else if (getValue(readString, '_', 1) == UBC_COMMAND_LED) {
    int t = getValue(readString, '_', 2).toInt();
    set_neopixel(t);
    //Serial.println("_led_"+String(t)+"_res_ok_");


  //}else if (getValue(readString, '_', 1) == UBC_COMMAND_HSV) {
   // int t = getValue(readString, '_', 2).toInt();
   // set_neopixel_hsv(t);
    //Serial.println("_hsv_" + String(t) + "_res_ok_");

}else if (getValue(readString, '_', 1) == "up") {
    digitalWrite(STATE_LED,HIGH);
    pos = 1;
}else if (getValue(readString, '_', 1) == "down") {
    digitalWrite(STATE_LED,LOW);
    pos = 150;
  }else if (getValue(readString, '_', 1) == UBC_COMMAND_SERVO) {
    pos = getValue(readString, '_', 2).toInt();
   
    
    myservo.write(pos);
    //myservo.attach(9); 

    //myservo.detach();
     //Serial.println("_servo_"+String(pos)+"_res_ok_");
  }


// Serial.println(readString);

  readString = "";
 // digitalWrite(STATE_LED,LOW);
}

 
  
 delay(1);
}

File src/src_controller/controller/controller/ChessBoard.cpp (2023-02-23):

#include "ChessBoard.h"

ChessBoard::ChessBoard() {

    if (!ConfigParser::getInstance()->configLoaded()) {
        LOG_F(ERROR, "CONFIG NOT LOADED");
    }

    if (!HardwareInterface::getInstance()->check_hw_init_complete()) {
        LOG_F(ERROR, "ChessBoard::ChessBoard HARDWARE INIT NOT COMPLETE LOADED");
    }
    //INIT BOARD ARRAYS => TO EMPY FIELDS
    initBoardArray(get_board_pointer(ChessBoard::BOARD_TPYE::TARGET_BOARD));
    initBoardArray(get_board_pointer(ChessBoard::BOARD_TPYE::REAL_BOARD));
    initBoardArray(get_board_pointer(ChessBoard::BOARD_TPYE::TEMP_BOARD));
}

ChessBoard::~ChessBoard() {
}

void ChessBoard::test_make_move_static() {
    MovePiar tmp_pair;
    HardwareInterface::getInstance()->home_sync();
    tmp_pair.from_field = ChessField::CHESS_FILEDS::CHESS_FIELD_G2;
    tmp_pair.to_field = ChessField::CHESS_FILEDS::CHESS_FIELD_A2;
    makeMoveSync(tmp_pair, false, false, false);
}

bool ChessBoard::test_make_move_func() {

    home_board();
    MovePiar tmp_pair;
    tmp_pair.from_field = ChessField::CHESS_FILEDS::CHESS_FIELD_H1;
    tmp_pair.to_field = ChessField::CHESS_FILEDS::CHESS_FIELD_PARK_POSTION_WHITE_1;
    makeMoveSync(tmp_pair, false, false, false);

    tmp_pair.from_field = ChessField::CHESS_FILEDS::CHESS_FIELD_E1;
    tmp_pair.to_field = ChessField::CHESS_FILEDS::CHESS_FIELD_A6;
    makeMoveSync(tmp_pair, false, false, false);

    tmp_pair.from_field = ChessField::CHESS_FILEDS::CHESS_FIELD_PARK_POSTION_WHITE_1;
    tmp_pair.to_field = ChessField::CHESS_FILEDS::CHESS_FIELD_E1;
    makeMoveSync(tmp_pair, false, false, false);

    tmp_pair.from_field = ChessField::CHESS_FILEDS::CHESS_FIELD_A6;
    tmp_pair.to_field = ChessField::CHESS_FILEDS::CHESS_FIELD_H1;
    makeMoveSync(tmp_pair, false, false, false);

    return true;
}

bool ChessBoard::MoveWaypointsAlong(std::queue<MV_POSITION> &_mv) {

    //LOAD CONFIG FOR MOVEMENT //TODO MOVE TO CONSTRUCTOR
    const bool EN_COIL_UPDATE_ALWAYS = ConfigParser::getInstance()->getBool_nocheck(
            ConfigParser::CFG_ENTRY::MECHANIC_WRITE_COIL_STATE_ALWAYS_MAKE_MOVE);
    const bool EN_COILE_ALWAYS_WRITE_OFF = ConfigParser::getInstance()->getBool_nocheck(
            ConfigParser::CFG_ENTRY::MECHANIC_WRITE_COIL_STATE_ALWAYS_WRITE_OFF);




    //SET MOTORS TO CHESS FIGURE MOVE SPEED
    HardwareInterface::getInstance()->set_speed_preset(HardwareInterface::HI_TRAVEL_SPEED_PRESET::HI_TSP_MOVE);

    //DISABLE COILS
    HardwareInterface::getInstance()->setCoilState(HardwareInterface::HI_COIL::HI_COIL_A, false);
    HardwareInterface::getInstance()->setCoilState(HardwareInterface::HI_COIL::HI_COIL_B, false);
    //ENABLE MOTOR
    HardwareInterface::getInstance()->enable_motors();
    bool is_first_move_in_sequence = true;
    int wait_counter = 0;
    bool ca_changed = false;
    bool cb_changed = false;
    while (!_mv.empty()) {
        //if (EN_COILE_ALWAYS_WRITE_OFF) {
         //   HardwareInterface::getInstance()->setCoilState(HardwareInterface::HI_COIL::HI_COIL_A, false);
         //   HardwareInterface::getInstance()->setCoilState(HardwareInterface::HI_COIL::HI_COIL_B, false);
        //}


        const MV_POSITION tmp = _mv.front();

        //SOME IMPROVEMENTS => SPI WRITING IS EXPENSIVE
        //if (EN_COIL_UPDATE_ALWAYS || ca_changed != tmp.coil_a_state) {
            //ca_changed = tmp.coil_a_state;
            HardwareInterface::getInstance()->setCoilState(HardwareInterface::HI_COIL::HI_COIL_A, tmp.coil_a_state);
        //}
        //if (EN_COIL_UPDATE_ALWAYS || cb_changed != tmp.coil_b_state) {
            //cb_changed = tmp.coil_b_state;
            HardwareInterface::getInstance()->setCoilState(HardwareInterface::HI_COIL::HI_COIL_B, tmp.coil_b_state);
        //}


        HardwareInterface::getInstance()->move_to_postion_mm_absolute(tmp.x, tmp.y,
                                                                      is_first_move_in_sequence);           //MOVE TO X AND NOT WAIT
        //WAIT FOR BOTH MOTORS TO FINISH
        // ADDITION ONLY WAIT AT THE LAST MOVEMENT STEP
        // SO MOVES BETWEEN CAN BE QUEUED IN MARLIN

        if(_mv.size() == 1 || !HardwareInterface::getInstance()->is_production_hardware()){
            while (!(HardwareInterface::getInstance()->is_target_position_reached())) {
                std::this_thread::sleep_for(std::chrono::milliseconds(WAITITME_FOR_MOTORS_TO_ARRIVE));
            }
        }
        _mv.pop();

        if(is_first_move_in_sequence){
            is_first_move_in_sequence = false;
        }
    }
    //DISBALE MOTOR
    HardwareInterface::getInstance()->disable_motors();
    //DISABLE COILS
    HardwareInterface::getInstance()->setCoilState(HardwareInterface::HI_COIL::HI_COIL_A, false);
    HardwareInterface::getInstance()->setCoilState(HardwareInterface::HI_COIL::HI_COIL_B, false);

    return true;
}
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

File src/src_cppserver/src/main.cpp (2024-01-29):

#include <iostream>
#include <cstdio>

#ifdef __MACH__
#include <mach/clock.h>
#include <mach/mach.h>
#endif


#include <chrono>
#include <algorithm>

#include "SHARED/loguru-master/loguru.hpp"
#include "SHARED/cpp-httplib-master/httplib.h"
#include "SHARED/json11-master/json11.hpp"
#include "SHARED/magic_enum-master/include/magic_enum.hpp"

#include <fmt/core.h>

#include "helper.h"
#include "SQLITE3_QUERY.hpp"
#include "SQLITE3.hpp"
#include "ConfigParser.h"

#include <thc.h>



#include "THIRDPARTY/uciadapter/src/UCI.cpp"

#define LOG_FILE_PATH_ERROR "./atcserver_error_log.log"
#define LOG_FILE_PATH "./atcserver_log.log"
#define DEFAULT_CONFIG_FILE_PATH "./atcserverconfig.ini"
#define GAMEDATA_DATABASE_NAME "gamedata"
#define SYSTEM_TICK_DELAY 100

#ifndef VERSION
#define VERSION "1.0.0"
#endif


volatile bool main_thread_running = false;

void signal_callback_handler(int signum) {
    printf("Caught signal %d\n", signum);

    LOG_F(ERROR, "Caught signal %d\n", signum);
    loguru::flush();
    main_thread_running = false;
    //exit(signum);
}


typedef std::chrono::high_resolution_clock Clock;
typedef std::chrono::system_clock::time_point TimePoint;
#define CHRONO_DURATION_MS(x, y) std::chrono::duration_cast<std::chrono::milliseconds>(x - y).count()


#ifdef __MACH__
struct timespec t1;
struct timespec t2;
#else
TimePoint t1 = Clock::now();
TimePoint t2 = Clock::now();
#endif

void sys_tick_delay() {
#ifdef __MACH__
    clock_serv_t cclock;
    mach_timespec_t mts;
    host_get_clock_service(mach_host_self(), CALENDAR_CLOCK, &cclock);
    clock_get_time(cclock, &mts);
    mach_port_deallocate(mach_task_self(), cclock);
    t2.tv_sec = mts.tv_sec;
    t2.tv_nsec = mts.tv_nsec;
    // IF TIME DIFFERENCE IS BIG ENOUGHT => CALL THE TIMER EVENT
    if ((t2.tv_sec - t1.tv_sec) > SYSTEM_TICK_DELAY) {
        host_get_clock_service(mach_host_self(), CALENDAR_CLOCK, &cclock);
        clock_get_time(cclock, &mts);
        mach_port_deallocate(mach_task_self(), cclock);
        t1.tv_sec = mts.tv_sec;
        t1.tv_nsec = mts.tv_nsec;
#else
    t2 = Clock::now();
    // IF TIME DIFFERENCE IS BIG ENOUGHT => CALL THE TIMER EVENT
    if (CHRONO_DURATION_MS(t2, t1) > SYSTEM_TICK_DELAY) {
        t1 = Clock::now();
#endif
    }
}

enum class AI_ALGORITHMS {
    RNG = 0,
    FIRST = 1,
    CUSTOM = 2
};

enum class GAME_STATE {
    PS_INVALID = 0,
    PS_IDLE = 1,
    PS_SEARCHING = 4,
    PS_SEARCHING_MANUAL = 5,
    PS_PREPARING_INGAME = 6,
    PS_INGAME = 7,
    PS_GAME_OVER = 8
};

struct GAME_DB_ENTRY_READ {
    bool valid = false;
    std::string hwid;
    std::string sid;
    GAME_STATE game_state = GAME_STATE::PS_INVALID;
    bool remote_player_is_white = false;
    bool is_syncing_phase = false;
    std::string current_board_fen;
    bool waiting_for_game = false;
    bool game_running = false;
    bool is_game_over = false;
    std::string game_id;
};


bool update_game_db_entry(SQLITE3 &_db, const std::string &_hwid = "", const std::string &_sid = "",
                          const std::string &_game_state = "", const std::string &_remote_player_is_white = "",
                          const std::string &_is_syncing_phase = "", const std::string &_current_board_fen = "") {

    std::string q = fmt::format("UPDATE {} SET", GAMEDATA_DATABASE_NAME);
    bool updated = false;
    if (!_sid.empty()) {
        q += fmt::format(" SID='{}',", _sid);
        updated = true;
    }

    if (!_game_state.empty()) {
        q += fmt::format(" game_state={},", _game_state);
        updated = true;
    }

    if (!_remote_player_is_white.empty()) {
        q += fmt::format(" remote_player_is_white={},", _remote_player_is_white);
        updated = true;
    }

    if (!_is_syncing_phase.empty()) {
        q += fmt::format(" is_syncing_phase={},", _is_syncing_phase);
        updated = true;
    }

    if (!_current_board_fen.empty()) {
        q += fmt::format(" current_board_fen='{}',", _current_board_fen);
        updated = true;
    }

    // REMOVE FINAL ','
    q.pop_back();


    if (!_hwid.empty()) {
        q += fmt::format(" WHERE HWID='{}'", _hwid);
    }



    //EXECUTE QUERY
    if (updated) {
        SQLITE3_QUERY update_query = SQLITE3_QUERY(q); // ? will be replaced after bind
        if (_db.execute(update_query) || _db.commit()) { // execute query
            _db.perror();
            return false;
        }
    }
    return true;
}


std::vector<GAME_DB_ENTRY_READ>
get_game_db_entry(SQLITE3 &_db, const std::string &_hwid = "", const std::string &_sid = "") {
    std::vector<GAME_DB_ENTRY_READ> res;
    std::string q = "SELECT game_state, remote_player_is_white, is_syncing_phase, current_board_fen, HWID, SID FROM ?";

    if (!_hwid.empty() || !_sid.empty()) {
        q += "WHERE ";
    }
    if (!_hwid.empty()) {
        q += fmt::format("HWID='{}' ", _hwid);
    }

    if (!_hwid.empty() && !_sid.empty()) {
        q += "AND ";
    }

    if (!_sid.empty()) {
        q += fmt::format("SID='{}' ", _sid);
    }


    SQLITE3_QUERY query = SQLITE3_QUERY(q);
    query.add_binding(GAMEDATA_DATABASE_NAME);
    if (!_db.execute(query) && !_db.get_result_row_count() <= 0) {

#ifdef  DEBUG
        _db.print_result();
#endif

        const auto qres = _db.copy_result();
        for (auto e: *qres) {
            GAME_DB_ENTRY_READ result_entry = GAME_DB_ENTRY_READ();
            result_entry.valid = true;
            result_entry.game_state = magic_enum::enum_cast<GAME_STATE>(std::stoi(e.at(0))).value(); // game_state
            result_entry.remote_player_is_white = std::stoi(e.at(1));
            //     result_entry.is_syncing_phase = std::stoi(e.at(2));
            result_entry.current_board_fen = e.at(3);
            result_entry.hwid = e.at(4);
            result_entry.sid = e.at(5);


            result_entry.game_id = fmt::format("{}-{}", result_entry.hwid, result_entry.sid);

            if (result_entry.game_state == GAME_STATE::PS_SEARCHING ||
                result_entry.game_state == GAME_STATE::PS_SEARCHING_MANUAL) {
                result_entry.waiting_for_game = true;
            } else if (result_entry.game_state == GAME_STATE::PS_INGAME) {
                result_entry.game_running = true;
            } else if (result_entry.game_state == GAME_STATE::PS_GAME_OVER) {
                result_entry.is_game_over = true;
                result_entry.game_running = true;
            } else if (result_entry.game_state == GAME_STATE::PS_PREPARING_INGAME) {
                result_entry.is_syncing_phase = true;
                result_entry.game_running = true;
            }

            res.push_back(result_entry);
        }
    }

    return res;
}
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

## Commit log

2021-01-07 added 3d printing / laser files
    [ATC_12V_SOLANOID_15mm_1x.step, ATC_12V_SOLANOID_15mm_1x.stl, ATC_50x50_VSLOT_ROLLER_3x.step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]
2021-03-05 added marlinfw for skr1.4
2021-03-08 added src_controller
    [Anet A6 - SKR 1.3 motherboard case - 20 x 20 mounting.stl, Anet A6 - SKR 1.3 motherboard case.stl, Anet A6 - SKR 1.3 motherboard cover - 20 x 20 mounting.stl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]
2021-03-08 added src_server
    [pyvenv.cfg]
2021-03-09 added seconds timer
2021-03-11 added calibration coils siwtching
2021-03-11 added led color faq
2021-03-12 some readme
    [ATC_12V_SOLANOID_15mm_1x.step, ATC_12V_SOLANOID_15mm_1x.stl, ATC_50x50_VSLOT_ROLLER_3x.step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]
2021-03-17 better tex template
    [FigureMovementTimes.xlsx, FigureMovementTimes_ALGORITHM_COMPARE.xlsx]
2021-03-17 rm old template stuff
    [FigureMovementTimes.xlsx, FigureMovementTimes_ALGORITHM_COMPARE.xlsx]
2021-03-17 rm unused image
    [FigureMovementTimes.xlsx, FigureMovementTimes_ALGORITHM_COMPARE.xlsx]
2021-03-20 QT add parkpos buttons to cal screen gui
2021-03-21 FIX CALIBRATION SCREEN, AND ADDED SET_STEPS_MM FOR GCODE
    [Configuration.h]
2021-03-21 CALIBRATION SCREEN ADDING CELL SIZE CALIBRATION
2021-03-21 SKR1.4 TURBO SERVO FIRMWARE
    [Configuration.h, Configuration_adv.h]
2021-03-21 document changes of marlinfw
    [Configuration.h]
2021-03-22 added mechanic
    [2021_ATC_Y_Axis_Slider_Down v49.stl, 2021_ATC_guide_out_figures 1.stl, 2021_ATC_guide_out_figures 2.stl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]
2021-03-22 BUGFIX RESET EEPROM DURING STARTUP
    [ConfigParser.cpp, ConfigParser.h, GCodeSender.cpp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]
2021-03-26 CONTROLLER GUI added servo calibration screen
2021-03-26 SHARED fixing network erreor handling
    [ChessBoard.cpp, main.cpp]
2021-03-26 CONTROLLER added M150 rgb led support
2021-03-29 added userboard controller arduino src
2021-04-02 fixing ard project path
    [atc_io_controller.ino]
2021-04-06 nfc scan board working
2021-04-07 trave_to_field massive changes and bugfixes
    [ChessBoard.cpp, ChessBoard.h, UserBoardController.cpp]
2021-04-13 added fan control
2021-04-13 first scan board for move attembt
2021-04-14 added buggy autoscan feature
    [ConfigParser.cpp, ConfigParser.h]
2021-04-15 FIXING HUICOM HARD BUG config/upload/download log/upload/view working
    [ConfigParser.cpp]
2021-04-25 make scan button bigger
2021-04-30 added alexa skill configuration
    [fields_col-values.csv, fields_row-values.csv, figures-values.csv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]
2021-05-04 added pseudo legal move switch
2021-05-10 using init board
2021-05-10 updated api docu
    [move_validator_requests.csv, move_validator_requests.xlsx]
2021-05-11 added prop table
2021-06-08 Auto stash before merge of "master" and "origin/master"
    [commercial_chessboard_projects.xlsx]
2021-10-06 UBC: added servo command
2023-02-18 fixed ubc leds
2023-02-18 servo fixed
2023-02-19 nfc workaround using hse
    [userboardcontroller.ino]
2023-02-19 rgb fix for due version
    due only used in the bachelor thesis version of the table
    otherwise use a arduino mega
    [userboardcontroller.ino]
2023-02-20 updated ubc ws2811 pin
2023-02-20 50-usb.rules switched to devpath numbering
    marlin/skr => 1.6
    ubc = 1.7
2023-02-21 marlin skr 9600
    adn added autostart using inittab
    [Configuration.h]
2024-02-01 menu switching bug remains
    [ConfigParser.cpp]

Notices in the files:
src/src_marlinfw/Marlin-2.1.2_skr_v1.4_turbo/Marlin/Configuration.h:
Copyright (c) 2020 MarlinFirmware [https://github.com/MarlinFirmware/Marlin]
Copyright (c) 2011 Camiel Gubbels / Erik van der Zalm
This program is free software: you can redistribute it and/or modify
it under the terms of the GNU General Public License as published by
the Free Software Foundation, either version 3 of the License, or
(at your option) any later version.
